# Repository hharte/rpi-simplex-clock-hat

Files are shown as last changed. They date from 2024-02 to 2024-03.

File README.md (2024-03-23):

# RPi Simplex Clock Controller Hat

# Introduction

This project is a Raspberry Pi-compatible hat for controlling Simplex Synchronous clocks with a 24VAC motor and 24VAC correction solenoid.  This hardware can be used with the <code>[master-clock](https://github.com/hharte/master-clock.git)</code> software to implement a synchronous clock controller.

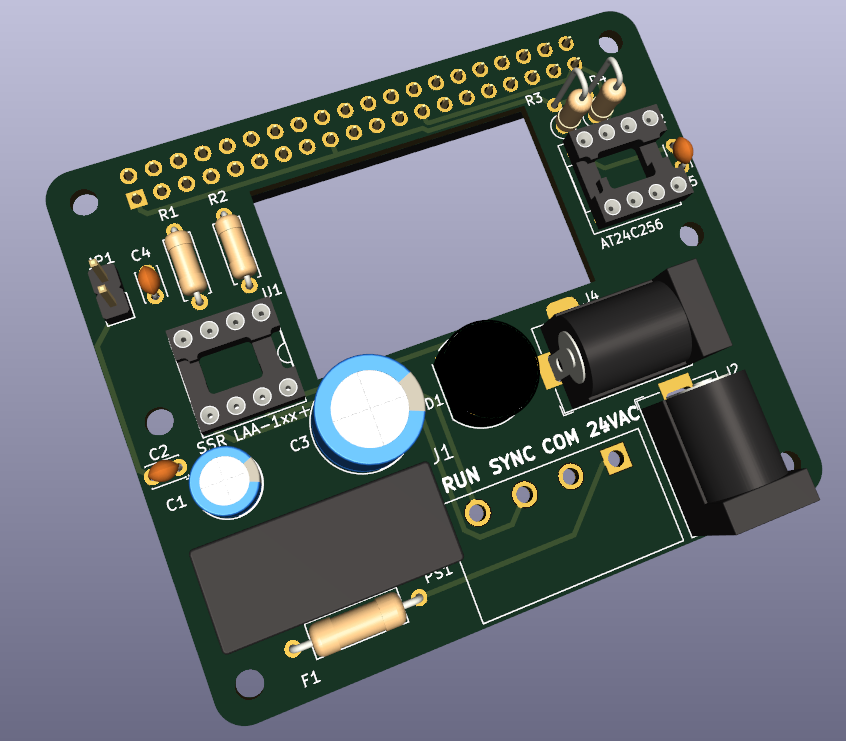
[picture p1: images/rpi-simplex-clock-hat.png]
image_tooltip


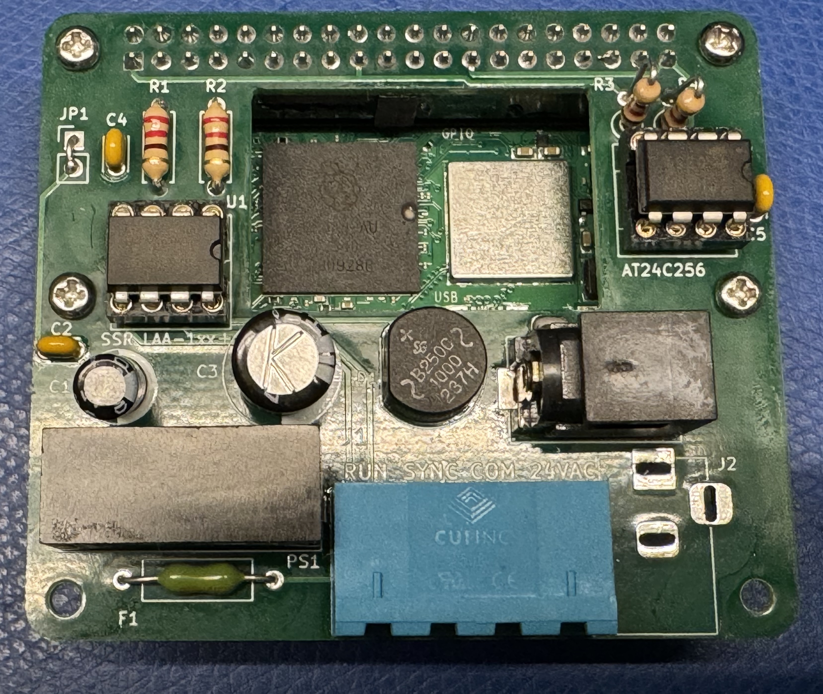
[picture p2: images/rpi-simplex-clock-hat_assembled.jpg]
image_tooltip


# Connectors

## Terminal block J1

<table>
  <tr>
   <td><strong><em>Pin</em></strong>
   </td>
   <td><strong><em>Name</em></strong>
   </td>
   <td><strong><em>Purpose</em></strong>
   </td>
  </tr>
  <tr>
   <td>1
   </td>
   <td>24VAC
   </td>
   <td>24VAC 60Hz Input
   </td>
  </tr>
  <tr>
   <td>2
   </td>
   <td>24VAC COM
   </td>
   <td>24VAC Common (Return)
   </td>
  </tr>
  <tr>
   <td>3
   </td>
   <td>SYNC
   </td>
   <td>24VAC Clock Sync Pulse Output
   </td>
  </tr>
  <tr>
   <td>4
   </td>
   <td>RUN
   </td>
   <td>24VAC Clock Motor control (optional)
   </td>
  </tr>
</table>

## Power Input Barrel Jacks J2, J4

Note: populate either J2 or J4.  J4 is intended to give the hat a smaller footprint when installed inside the clock housing.  J2 is intended for use with a full-size Raspberry Pi.

<table>
  <tr>
   <td><strong><em>Pin</em></strong>
   </td>
   <td><strong><em>Name</em></strong>
   </td>
   <td><strong><em>Purpose</em></strong>
   </td>
  </tr>
  <tr>
   <td>Tip
   </td>
   <td>24VAC
   </td>
   <td>24VAC 60Hz Input
   </td>
  </tr>
  <tr>
   <td>Ring
   </td>
   <td>24VAC COM
   </td>
   <td>24VAC Common (Return)
   </td>
  </tr>
</table>

Raspberry Pi J3 Signals

<table>
  <tr>
   <td><strong><em>Pin</em></strong>
   </td>
   <td><strong><em>Raspberry Pi Name</em></strong>
   </td>
   <td><strong><em>Purpose</em></strong>
   </td>
  </tr>
  <tr>
   <td>1
   </td>
   <td>3.3V DC Power
   </td>
   <td>3.3V DC Power
   </td>
  </tr>
  <tr>
   <td>2, 4
   </td>
   <td>5V DC Power
   </td>
   <td>Supplies 5VDC at 1.2A to backpower the RPi.
   </td>
  </tr>
  <tr>
   <td>11
   </td>
   <td>GPIO17
   </td>
   <td>SYNC
   </td>
  </tr>
  <tr>
   <td>13
   </td>
   <td>GPIO27
   </td>
   <td>RUN
   </td>
  </tr>
  <tr>
   <td>27
   </td>
   <td>ID_SDA
   </td>
   <td>ID EEPROM I2C Data
   </td>
  </tr>
  <tr>
   <td>28
   </td>
   <td>ID_SCL
   </td>
   <td>ID EEPROM I2C Clock
   </td>
  </tr>
</table>

# Power Supply

This board contains an AC to DC power supply to power the Raspberry Pi Zero 2 W from the same 24VAC that runs the clock motor.  If you do not wish to use this power supply to power the RPi, the following components may be omitted from your build:

<table>
  <tr>
   <td><strong><em>Reference Designator</em></strong>
   </td>
   <td><strong><em>Component</em></strong>
   </td>
  </tr>
  <tr>
   <td>D1
   </td>
   <td>Bridge rectifier
   </td>
  </tr>
  <tr>
   <td>C1, C2, C3, C4
   </td>
   <td>Capacitors
   </td>
  </tr>
  <tr>
   <td>PS1
   </td>
   <td>SPBW06-5 DC-DC Converter
   </td>
  </tr>
  <tr>
   <td>JP1
   </td>
   <td>Jumper
   </td>
  </tr>
</table>

# Jumper

When installed, JP1 provides 5VDC to the Raspberry Pi.  This hat can supply 5VDC at 1.2A, which is enough for a Raspberry Pi Zero 2W.

# Bill of Materials ([Interactive BOM](https://html-preview.github.io/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))

<table>
  <tr>
   <td><strong><em>Reference</em></strong>
   </td>
   <td><strong><em>Value</em></strong>
   </td>
   <td><strong><em>Quantity</em></strong>
   </td>
   <td><strong><em><a href="https://www.digikey.com/en/mylists/list/S3O64GTQV0">DigiKey</a></em></strong>
   </td>
   <td><strong><em><a href="https://www.mouser.com/ProjectManager/ProjectDetail.aspx?AccessID=516dae8649">Mouser</a></em></strong>
   </td>
  </tr>
  <tr>
   <td>C1
   </td>
   <td>10uF / 25V
   </td>
   <td>1
   </td>
   <td><a href="https://www.digikey.com/en/products/detail/panasonic-electronic-components/ECE-A1EN100UI/2689106">ECE-A1EN100UI</a>
   </td>
   <td><a href="https://www.mouser.com/ProductDetail/Panasonic/ECE-A1EN100UI?qs=0h1gzos03f36mGOUyzNXaA%3D%3D">ECE-A1EN100UI</a>
   </td>
  </tr>
  <tr>
   <td>C2,C4,C5
   </td>
   <td>0.1uF
   </td>
   <td>3
   </td>
   <td><a href="https://www.digikey.com/en/products/detail/kemet/C315C104M5U5TA7303/3726116">C315C104M5U5TA7303</a>
   </td>
   <td><a href="https://www.mouser.com/ProductDetail/KEMET/C315C104M5U5TA7303?qs=LRwtGMyvRhhtzW9z3Tp7qQ%3D%3D">C315C104M5U5TA7303</a>
   </td>
  </tr>
  <tr>
   <td>C3
   </td>
   <td>100uF / 100V
   </td>
   <td>1
   </td>
   <td><a href="https://www.digikey.com/en/products/detail/kyocera-avx/REF1016101M100K/20096922">REF1016101M100K</a>
   </td>
   <td><a href="https://www.mouser.com/ProductDetail/KYOCERA-AVX/REF1016101M100K?qs=Y0Uzf4wQF3nLwPgf4aAj8g%3D%3D">REF1016101M100K</a>
   </td>
  </tr>
  <tr>
   <td>D1
   </td>
   <td>B250C1000G-E4/51
   </td>
   <td>1
   </td>
   <td><a href="https://www.digikey.com/en/products/detail/vishay-general-semiconductor-diodes-division/B250C1000G-E4-51/2139752">B250C1000G-E4/51</a>
   </td>
   <td><a href="https://www.mouser.com/ProductDetail/625-B250C1000G-E4">625-B250C1000G-E4</a>
   </td>
  </tr>
  <tr>
   <td>F1
   </td>
   <td>630mA
   </td>
   <td>1
   </td>
   <td><a href="https://www.digikey.com/en/products/detail/littelfuse-inc/0251-630MAT1L/700712">F7846CT-ND</a>
   </td>
   <td><a href="https://www.mouser.com/ProductDetail/Littelfuse/0251.630MAT1L?qs=LpXnx4WbYtB1cmQ95xjPnQ%3D%3D">0251.630MAT1L</a>
   </td>
  </tr>
  <tr>
   <td>J1
   </td>
   <td>TBP01R1-508-04BE
   </td>
   <td>1
   </td>
   <td><a href="https://www.digikey.com/en/products/detail/cui-devices/TBP01R1-508-04BE/10238385">TBP01R1-508-04BE</a>
   </td>
   <td><a href="https://www.mouser.com/ProductDetail/CUI-Devices/TBP01R1-508-04BE?qs=PzGy0jfpSMtbuigPwCNi2Q%3D%3D"> TBP01R1-508-04BE</a>
   </td>
  </tr>
  <tr>
   <td>P1
   </td>
   <td>TBP01P1-508-04BE
   </td>
   <td>1
   </td>
   <td><a href="https://www.digikey.com/en/products/detail/cui-devices/TBP01P1-508-04BE/10238369">TBP01P1-508-04BE</a>
   </td>
   <td><a href="https://www.mouser.com/ProductDetail/CUI-Devices/TBP01P1-508-04BE?qs=PzGy0jfpSMudTtVMrQOyVQ%3D%3D">TBP01P1-508-04BE</a>
   </td>
  </tr>
  <tr>
   <td>J2,J4
   </td>
   <td>2.1mm Barrel
   </td>
   <td>1
   </td>
   <td><a href="https://www.digikey.com/en/products/detail/switchcraft-inc/RAPC722BK/1288776">RAPC722BK</a>
   </td>
   <td><a href="https://www.mouser.com/ProductDetail/Switchcraft/RAPC722BK?qs=Nl9mtr8tY%2Fsf3BOYJcSXfg%3D%3D">RAPC722BK</a>
   </td>
  </tr>
  <tr>
   <td>J3
   </td>
   <td>2x20 female
   </td>
   <td>1
   </td>
   <td><a href="https://www.digikey.com/en/products/detail/samtec-inc/SSQ-120-01-F-D/6678748">SSQ-120-01-F-D</a>
   </td>
   <td><a href="https://www.mouser.com/ProductDetail/200-SSQ12001FD">SSQ-120-01-F-D</a>
   </td>
  </tr>
  <tr>
   <td>JP1
   </td>
   <td>Short with wire.
   </td>
   <td>-
   </td>
   <td>-
   </td>
   <td>-
   </td>
  </tr>
  <tr>
   <td>PS1
   </td>
   <td>SPBW06-05
   </td>
   <td>1
   </td>
   <td><a href="https://www.digikey.com/en/products/detail/mean-well-usa-inc/SPBW06F-05/7707011">SPBW06F-05</a>
   </td>
   <td><a href="https://www.mouser.com/ProductDetail/709-SPBW06G-05">709-SPBW06G-05</a>
   </td>
  </tr>
  <tr>
   <td>R1,R2
   </td>
   <td>220 ohm
   </td>
   <td>2
   </td>
   <td><a href="https://www.digikey.com/en/products/detail/stackpole-electronics-inc/CFM12JT220R/1741901">CFM12JT220R</a>
   </td>
   <td><a href="https://www.mouser.com/ProductDetail/YAGEO/CFR-25JR-52-220K?qs=KUIzHt%2Fe91nHT%2FPpMV7tqA%3D%3D">CFR-25JR-52-220</a>
   </td>
  </tr>
  <tr>
   <td>R3,R4
   </td>
   <td>3.9K ohm
   </td>
   <td>2
   </td>
   <td><a href="https://www.digikey.com/en/products/detail/stackpole-electronics-inc/CFM12JT3K90/1741927">S3.9KHCT-ND</a>
   </td>
   <td><a href="https://www.mouser.com/ProductDetail/YAGEO/CFR-25JR-52-3K9?qs=19cKSROHwrB%2FJo8M8ItsUQ%3D%3D">CFR-25JR-52-3K9</a>
   </td>
  </tr>
  <tr>
   <td>U1
   </td>
   <td>LAA108
   </td>
   <td>1
   </td>
   <td><a href="https://www.digikey.com/en/products/detail/ixys-integrated-circuits-division/LAA108/3077633">LAA108</a>
   </td>
   <td><a href="https://www.mouser.com/ProductDetail/IXYS-Integrated-Circuits/LAA108?qs=OpMkDkHXivMke3NLFDg0nw%3D%3D">849-LAA108</a>
   </td>
  </tr>
  <tr>
   <td>U2
   </td>
   <td>24LC256
   </td>
   <td>1
   </td>
   <td><a href="https://www.digikey.com/en/products/detail/microchip-technology/24LC64-I-P/273427">24LC64-I/P</a>
   </td>
   <td><a href="https://www.mouser.com/ProductDetail/Microchip-Technology/24LC64-I-P?qs=EkZBwCRGcSvc%252BCDluHmdqw%3D%3D">24LC64-I/P</a>
   </td>
  </tr>
  <tr>
   <td>
   </td>
   <td>8-pin DIP Sockets
   </td>
   <td>2
   </td>
   <td><a href="https://www.digikey.com/en/products/detail/assmann-wsw-components/AR-08-HZL-TT/821765">AR 08-HZL-TT</a>
   </td>
   <td><a href="https://www.mouser.com/ProductDetail/Mill-Max/110-41-308-41-001000?qs=dvxwXVM4mZVj1CY1TePuww%3D%3D">110-41-308-41-001000</a>
   </td>
  </tr>
</table>

# Hat ID EEPROM

The board contains a footprint for a 24C256 or similar serial EEPROM.  This EEPROM connects to the Raspberry Pi’s i2c-0 port, and contains configuration data describing the hat.

The i2c-0 port needs to be enabled in `/boot/config.txt` by manually adding the line:

```
dtparam=i2c_vc=on
```

And uncommenting:

```
dtparam=i2c_arm=on
```

Reboot the Pi and make sure the EEPROM is detected at address 0x50:

```
$ i2cdetect -y 0
     0  1  2  3  4  5  6  7  8  9  a  b  c  d  e  f
00:                         -- -- -- -- -- -- -- --
10: -- -- -- -- -- -- -- -- -- -- -- -- -- -- -- --
20: -- -- -- -- -- -- -- -- -- -- -- -- -- -- -- --
30: -- -- -- -- -- -- -- -- -- -- -- -- -- -- -- --
40: -- -- -- -- -- -- -- -- -- -- -- -- -- -- -- --
50: 50 -- -- -- -- -- -- -- -- -- -- -- -- -- -- --
60: -- -- -- -- -- -- -- -- -- -- -- -- -- -- -- --
70: -- -- -- -- -- -- -- --
```

Use utilities from here: [https://github.com/raspberrypi/hats](https://github.com/raspberrypi/hats)

```
$ git clone https://github.com/raspberrypi/hats
$ cd hats/eepromutils/
$ make
$ ./eepmake rpi-simplex-clock-hat.txt rpi-simplex-clock-hat.eep
$ sudo ./eepflash.sh -w -f=./rpi-simplex-clock-hat.eep -t=24c64 -d=0
This will attempt to talk to an eeprom at i2c address 0x50. Make sure there is an eeprom at this address.
This script comes with ABSOLUTELY no warranty. Continue only if you know what you are doing.
Do you wish to continue? (yes/no): yes
Writing...
0+1 records in
0+1 records out
149 bytes copied, 0.660765 s, 0.2 kB/s
Closing EEPROM Device.
Done.
```

Read EEPROM to a file:

```
sudo ./eepflash.sh -r -t=24c64 -f=readout.eep
```

After programming the EEPROM and rebooting, the hat information should be available in `/proc/device-tree/hat/`

# Mounting Brackets

3D-printable mounting brackets for the [Raspberry Pi Zero 2 W](https://github.com/hharte/rpi-simplex-clock-hat/blob/main/mounting/rpi-zero-simplex-clock-mounting.stl) and [full-size Raspberry Pi](https://github.com/hharte/rpi-simplex-clock-hat/blob/main/mounting/rpi-simplex-clock-mounting.stl) are provided.  The Raspberry Pi Zero 2 W can fit inside the clock movement housing.

# Software Installation

The software for this project consists of Raspberry Pi OS as well as a [Master Clock Daemon](https://github.com/hharte/master-clock.git) which is a Python script that activates the SYNC output at the correct times for hourly and 12-hour corrections.

## Raspberry Pi Zero 2 W

Install Raspberry Pi OS to MicroSD card using Raspberry Pi Imager.  Select Raspberry Pi OS (other) → Raspberry Pi OS (Legacy, 32-bit) Lite.

Change settings to enable WiFi with SSID/Password, set WiFi country, set locale, set username/password.

After booting the Raspberry Pi, ssh in and:

```
$ sudo apt-get install ntpdate
$ sudo ntpdate time.google.com
$ sudo apt-get update; sudo apt-get upgrade
$ sudo apt-get install git gpiod i2c-tools
$ git clone https://github.com/hharte/master-clock.git
```

### Configure Service

Edit `simplex_master_clock.service` and change the following line to the correct path for `simplex_master_clock.py`:

ExecStart=/usr/bin/python3 /home/pi/master-clock/simplex_master_clock.py

### Install Service

```
$ sudo cp simplex_master_clock.service /etc/systemd/system/
$ sudo systemctl enable simplex_master_clock.service
$ sudo systemctl start simplex_master_clock.service
$ sudo systemctl status simplex_master_clock.service
```

# Clock Connectors

The Simplex synchronous clocks typically have a 4-pin female Molex MLX connector.  These connectors, pins, and tools are available from Amazon:

Connectors: [https://www.amazon.com/dp/B07DKZQK5M](https://www.amazon.com/dp/B07DKZQK5M)

Crimper: [https://www.amazon.com/gp/product/B0C8MXNWDK](https://www.amazon.com/gp/product/B0C8MXNWDK)

Pin Extractor: DAP-T292328: [https://www.amazon.com/dp/B0C4NWRQD4](https://www.amazon.com/dp/B0C4NWRQD4)

# Clock Movement Bushings

The clock movements are mounted using pins with spring clips and rubber bushings.  These rubber bushings become dried out and brittle with age.  If you would like to replace them, the ¼” grommets in this kit work well: [300 Pcs Rubber Grommets Kit](https://www.amazon.com/gp/product/B0BXKXMT55).

# Compatibility with other Pi Hats

The synchronous clock controller is designed to support piggybacking with the [Uputronics Pi GPS/RTC Expansion Board](https://store.uputronics.com/index.php?route=product/product&product_id=81).  When used in conjunction with the GPS Expansion Board, a complete accurate time solution can be realized.

# Revision History

Rev 0 → Rev 1

1. Turn SSRs on with logic 1 to GPIO outputs.  This is needed so that the SSRs don't become enabled when the GPIO17 and GPIO27 are set to outputs during boot.  These GPIOs are pulled low on the RPi.
2. Add alternate footprint location (J4) for AC input barrel jack.
3. Add additional mounting holes for Raspberry Pi Zero / Zero 2 W.
4. Correct pinout for the bridge rectifier D1.

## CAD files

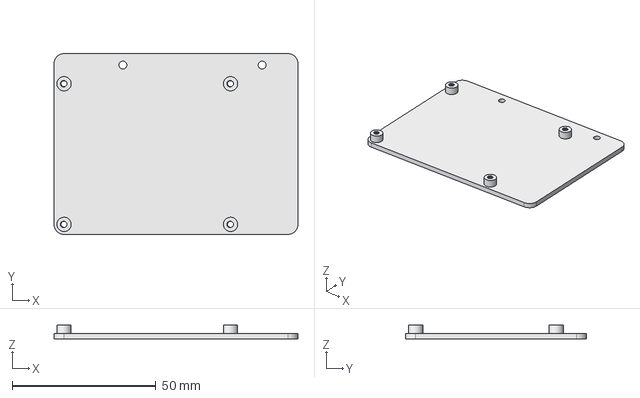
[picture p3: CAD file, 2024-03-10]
mounting/rpi-simplex-clock-mounting.FCStd
85.0 x 63.0 x 5.00 mm

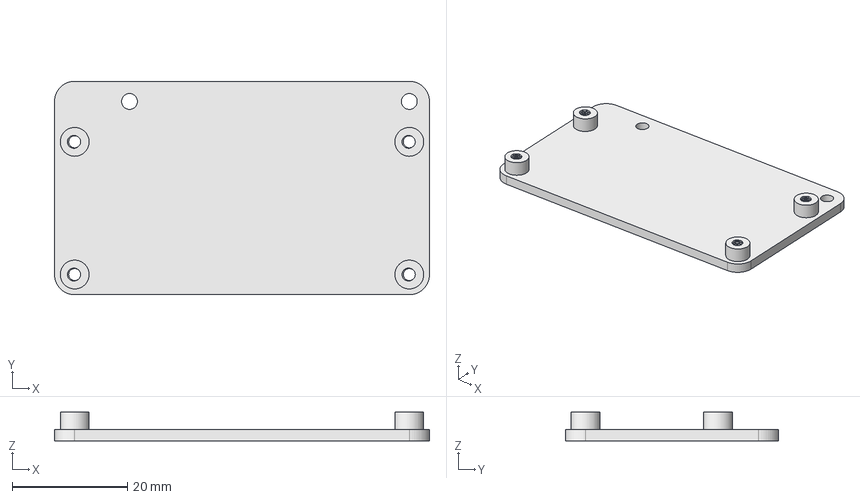
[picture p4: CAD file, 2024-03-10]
mounting/rpi-zero-simplex-clock-mounting.FCStd
65.0 x 37.0 x 5.00 mm

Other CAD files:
mounting/rpi-simplex-clock-mounting.stl
mounting/rpi-zero-simplex-clock-mounting.stl

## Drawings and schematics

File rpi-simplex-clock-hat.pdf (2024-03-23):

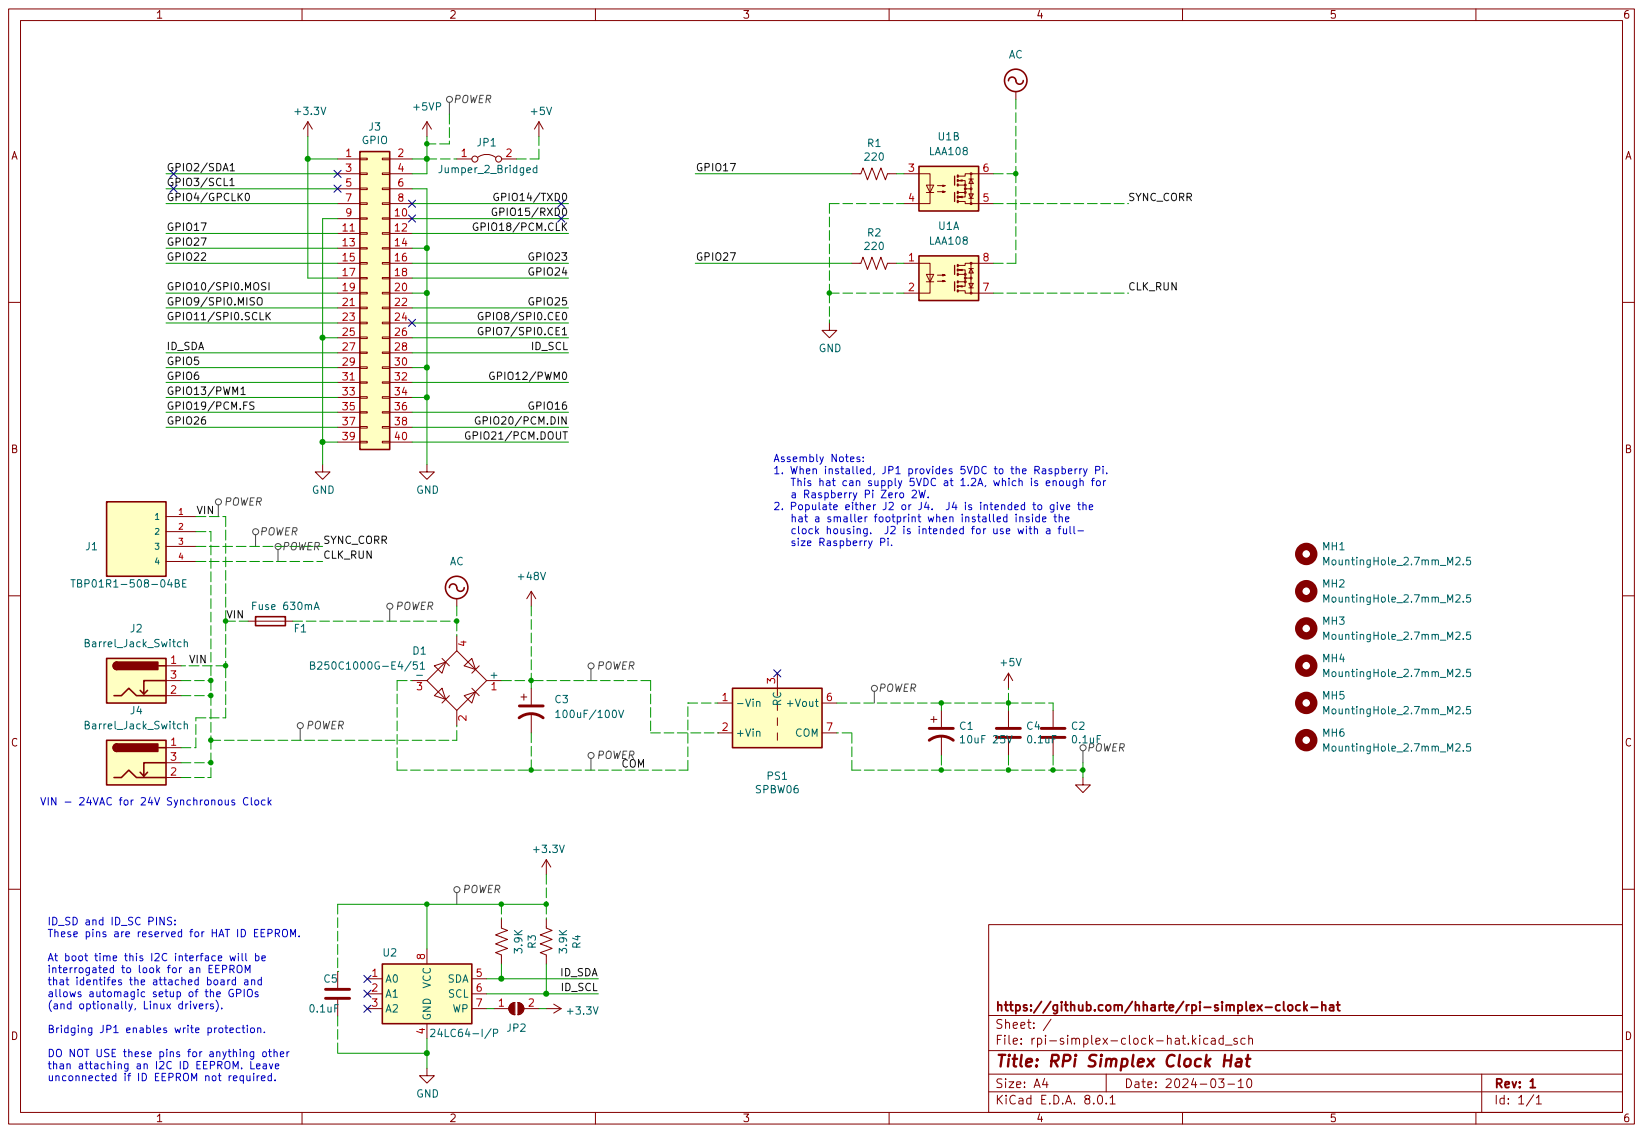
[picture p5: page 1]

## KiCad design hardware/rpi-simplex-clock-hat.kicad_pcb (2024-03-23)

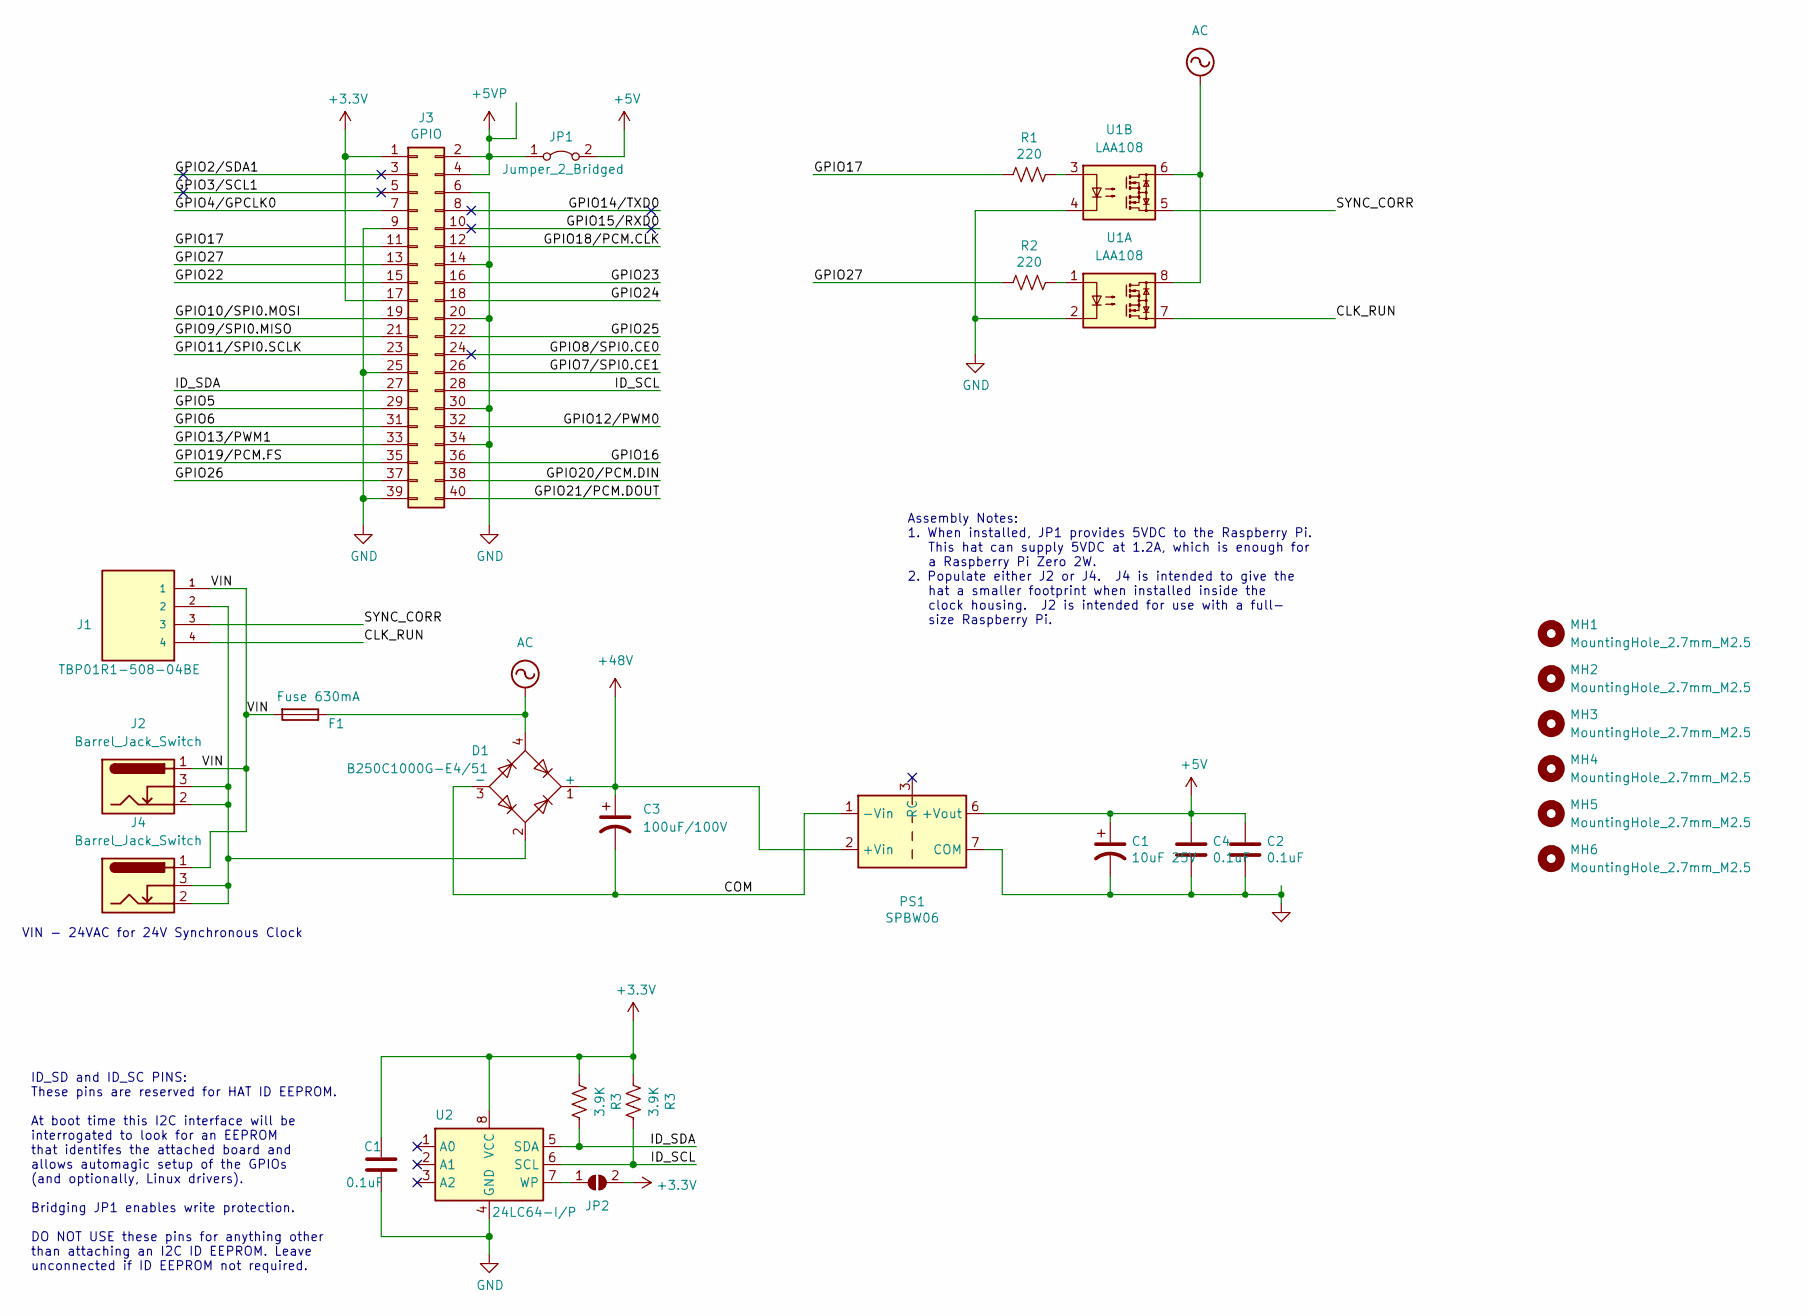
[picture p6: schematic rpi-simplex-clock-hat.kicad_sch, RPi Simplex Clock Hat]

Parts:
C1, C2, C4: 0.1uF; C_Disc_D3.0mm_W2.0mm_P2.50mm; MPN C315C104M5U5TA7303
C3: 100uF/100V; CP_Radial_D10.0mm_P5.00mm; MPN REF1016101M100K
D1: B250C1000G-E4/51; Diode_Bridge_Round_D9.8mm; MPN B250C1000G-E4/51
F1: Fuse 630mA; R_Axial_DIN0309_L9.0mm_D3.2mm_P12.70mm_Horizontal; MPN 0251.630MAT1L
J1: TBP01R1-508-04BE; CUI_TBP01R1-508-04BE; MPN TBP01R1-508-04BE
J2, J4: Barrel_Jack_Switch; BarrelJack_Horizontal; MPN RAPC722BK
J3: GPIO; PinSocket_2x20_P2.54mm_Vertical; MPN SSQ-120-01-F-D
JP1: Jumper_2_Bridged; PinHeader_1x02_P2.54mm_Vertical
JP2: ID_WP; SolderJumper-2_P1.3mm_Open_Pad1.0x1.5mm
MH1, MH2, MH3, MH4, MH5, MH6: MountingHole_2.7mm_M2.5
PS1: SPBW06; Converter_DCDC_TRACO_TMR-xxxx_THT; MPN SPBW06F-05
R1, R2: 220; R_Axial_DIN0207_L6.3mm_D2.5mm_P7.62mm_Horizontal; MPN CFM12JT220R
R3: 3.9K; R_Axial_DIN0207_L6.3mm_D2.5mm_P2.54mm_Vertical; MPN CFM12JT3K90
U1: LAA108; DIP-8_W7.62mm_Socket; MPN LAA108
U2: 24LC64-I/P; DIP-8_W7.62mm_Socket; MPN 24LC64-I/P

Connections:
+5VP: J3.2, J3.4, JP1.1 (A)
+48V: C3.1, D1.1 (+), PS1.2 (+Vin)
/CLK_RUN: J1.4, U1.7
/COM: C3.2, D1.3 (-), PS1.1 (-Vin)
/GPIO2/SDA1: J3.3
/GPIO3/SCL1: J3.5
/GPIO4/GPCLK0: J3.7
/GPIO5: J3.29
/GPIO6: J3.31
/GPIO7/SPI0.CE1: J3.26
/GPIO8/SPI0.CE0: J3.24
/GPIO9/SPI0.MISO: J3.21
/GPIO10/SPI0.MOSI: J3.19
/GPIO11/SPI0.SCLK: J3.23
/GPIO12/PWM0: J3.32
/GPIO13/PWM1: J3.33
/GPIO14/TXD0: J3.8
/GPIO15/RXD0: J3.10
/GPIO16: J3.36
/GPIO17: J3.11, R1.2
/GPIO18/PCM.CLK: J3.12
/GPIO19/PCM.FS: J3.35
/GPIO20/PCM.DIN: J3.38
/GPIO21/PCM.DOUT: J3.40
/GPIO22: J3.15
/GPIO23: J3.16
/GPIO24: J3.18
/GPIO25: J3.22
/GPIO26: J3.37
/GPIO27: J3.13, R2.2
/SYNC_CORR: J1.3, U1.5
/VIN: F1.2, J1.1, J2.1, J4.1
AC: D1.4, F1.1, U1.6, U1.8
GND: C1.2, C2.2, C4.2, J3.6, J3.9, J3.14, J3.20, J3.25, J3.30, J3.34, J3.39, PS1.7 (COM), U1.2, U1.4, U2.4 (GND); also elsewhere on the board
unnamed: D1.2, J1.2, J2.2, J2.3, J4.2, J4.3
unnamed: JP2.1 (A), U2.7 (WP)
unnamed: R1.1, U1.3
unnamed: R2.1, U1.1

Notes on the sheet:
VIN - 24VAC for 24V Synchronous Clock
Assembly Notes: 1. When installed, JP1 provides 5VDC to the Raspberry Pi. This hat can supply 5VDC at 1.2A, which is enough for a Raspberry Pi Zero 2W. 2. Populate either J2 or J4. J4 is intended to give the hat a smaller footprint when installed inside the clock housing. J2 is intended for use wit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
ID_SD and ID_SC PINS: These pins are reserved for HAT ID EEPROM. At boot time this I2C interface will be interrogated to look for an EEPROM that identifes the attached board and allows automagic setup of the GPIOs (and optionally, Linux drivers). Bridging JP1 enables write protection. DO NOT USE th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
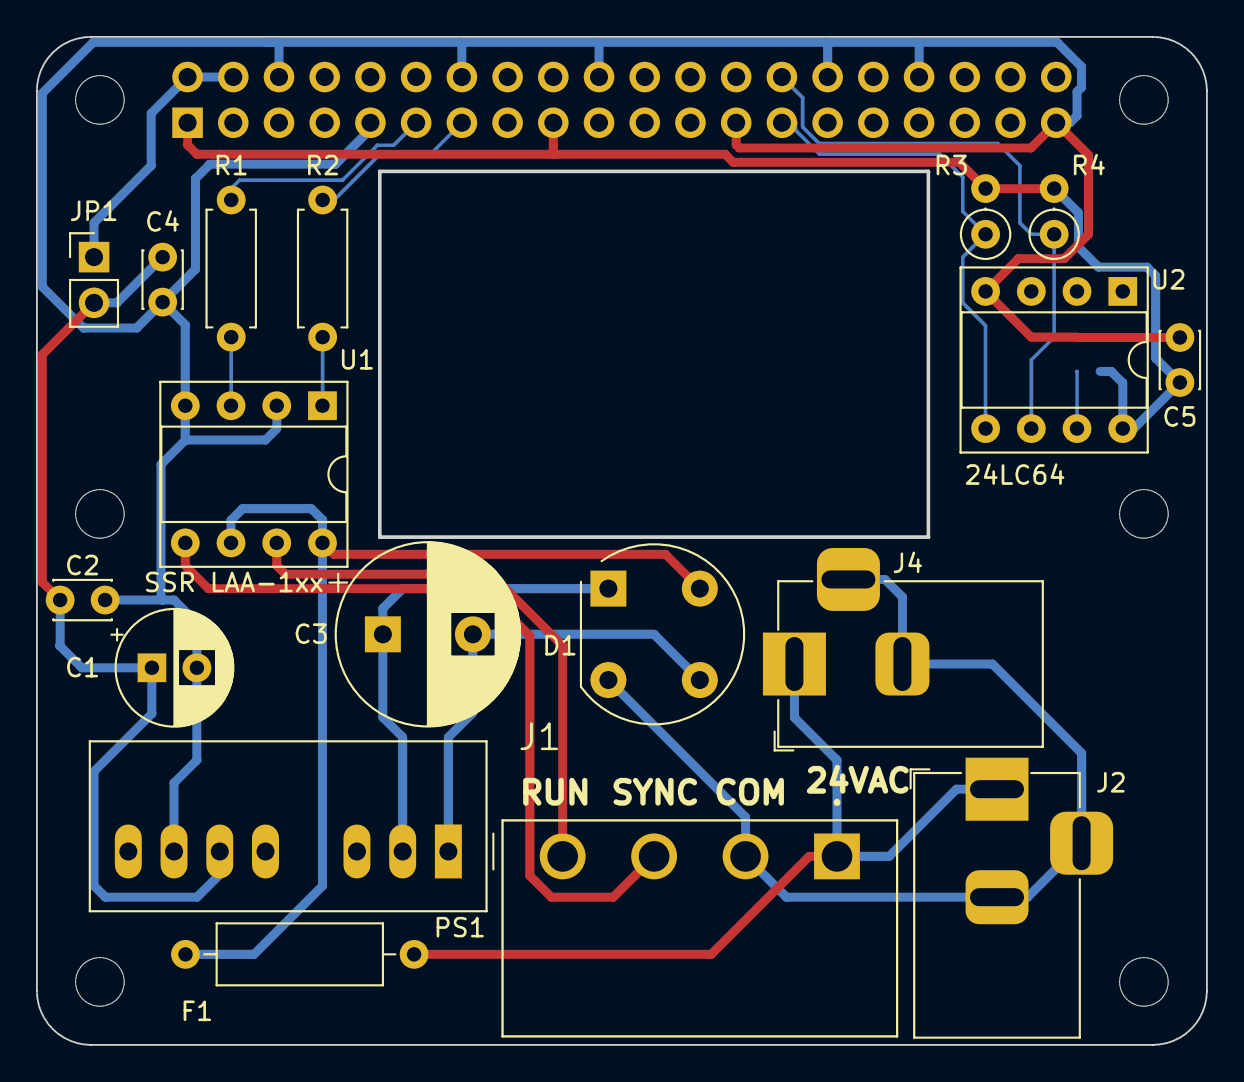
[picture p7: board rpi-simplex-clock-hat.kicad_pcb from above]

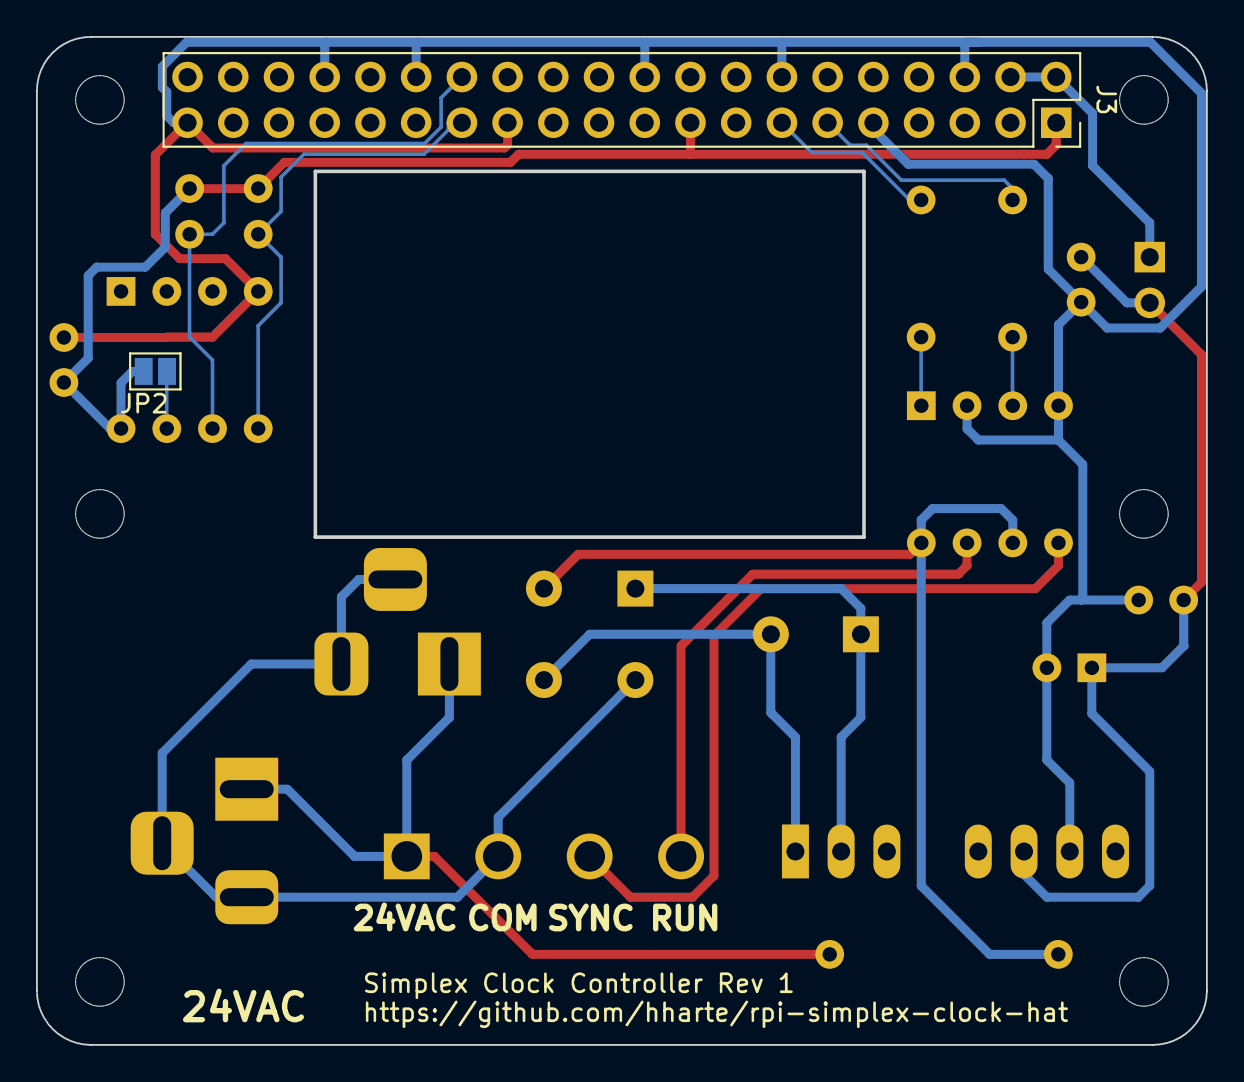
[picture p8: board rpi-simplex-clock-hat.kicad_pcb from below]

Board: 2 copper layers, 65.0 x 56.0 mm, 26 parts (2 on the bottom side), 18 nets.

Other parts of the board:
C5: 0.1uF; C_Disc_D3.0mm_W2.0mm_P2.50mm
R4: 3.9K; R_Axial_DIN0207_L6.3mm_D2.5mm_P2.54mm_Vertical

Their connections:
GND: C5.2; also elsewhere on the board

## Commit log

2024-02-04 Initial Rev 0 version, fabbed out 2024-02-03.
    [rpi-simplex-clock-hat-B_Cu.gbr, rpi-simplex-clock-hat-B_Mask.gbr, rpi-simplex-clock-hat-B_Silkscreen.gbr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]
2024-02-17 Rev 1: Fix minor issues in Rev 0.
    1. Turn SSRs on with logic 1 to GPIO outputs. This is needed so that
    the SSRs don't become enabled when the GPIO17 and GPIO27 are set to
    outputs. These GPIOs are pulled low.
    2. Add alternate footprint location (J4) for AC input barrel jack.
    3. Add additional mounting holes for Raspberry Pi Zero / Zero 2 W.
    4. Correct pinout for the bridge rectifier D1.
    [rpi-simplex-clock-hat-B_Cu.gbr, rpi-simplex-clock-hat-B_Mask.gbr, rpi-simplex-clock-hat-B_Silkscreen.gbr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]
2024-03-10 Mounting plates for RPi Zero 2W and full-size RPi.
    [rpi-simplex-clock-mounting.FCStd, rpi-simplex-clock-mounting.stl, rpi-zero-simplex-clock-mounting.FCStd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]
2024-03-10 Update for KiCAD 8.0
    [rpi-simplex-clock-hat.kicad_pcb, rpi-simplex-clock-hat.kicad_sch]
2024-03-23 Add interactive BOM, update to KiCAD 8.0.1.
    [rpi-simplex-clock-hat-B_Cu.gbr, rpi-simplex-clock-hat-B_Mask.gbr, rpi-simplex-clock-hat-B_Silkscreen.gbr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]
